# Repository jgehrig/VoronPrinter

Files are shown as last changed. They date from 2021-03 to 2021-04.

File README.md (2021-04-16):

# VoronPrinter
Build Logs, Notes, and Design Modifications for a Voron 3D Printer

## Cura Slicer Setup
[Cura Slicer Configuration](config/cura)

## Extended Feet
[Extended Printer Feet](mods/extended_feet)

## Power Entry Connector
[Power Entry Connector MountPCB](mods/power_entry)

## Wiring PCB
[Wiring Helper PCB](mods/wiring_pcb)

## X Gantry Endstop
[Adjustable X Gantry Endstop](mods/x_gantry_endstop)

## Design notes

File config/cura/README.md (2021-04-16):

# Voron V0 Cura Configuration
Setup instructions for Cura and the Voron V0.

Cura Screenshot with Voron Test Cube

These instructions were tested on Linux and Cura 4.8, they should also work on MacOS/Windows.

## Copy Configuration Folder
Find the Cura `Configuration Folder`:
 1. Open Cura.
 2. Using the file menu, `Help -> Configuration Folder`
 3. The `Configuration Folder` will open in your file manager

On Linux, the configuration folder is: `~/.config/cura/{cura_version}/`.

Simply copy the contents `cura-config-folder` from this repository into the path above.

## Adding Your Printer
Creates an instance of your printer in Cura.

Note, the Configuration Folder step above must be done before proceeding with the steps below.

Add your printer to Cura:
 1. In the file menu, `Settings -> Printer -> Add Printer...`.
 2. Select, `A non-networked printer -> VoronDesign -> VORON V0`.
 3. Type a unique `Printer name` in the text box on the right.
 4. Click the `Add` button.
 5. Set the `G-code flavor` dropdown to `Marlin`
 6. Paste your Start G-code, see [Startup GCode](#Startup-GCode).
 7. Modify any settings, the defaults should be fine.
 8. Click the `Next` button.
 9. You should see your pinter in the dropdown.

Screenshots:

Cura Add Printer Dialog <br />
Cura Machine Settings Dialog <br />
Cura Printer Dropdown <br />

## Printer Definition
Basic information about the printer is defined in:

`{cura_config_folder}/definitions/voron0_120.def.json`

```
{
    "name": "VORON V0",
    "version": 0,
    "inherits": "voron2_base",
    "metadata":
    {
        "visible": true,
        "platform": "V0_120mm_Bed.stl",
        "quality_definition": "voron2_base"
    },
    "overrides":
    {
        "machine_name":     { "default_value": "VORON V0" },
        "machine_width":    { "default_value": 120 },
        "machine_depth":    { "default_value": 120 },
        "machine_height":   { "default_value": 120 }
    }
}
```

## Print Platform 3D Model
The 3D model is definied in:

`{cura_config_folder}/meshes/V0_120mm_Bed.stl`

The STL model is courtesy of [hartk1213](https://github.com/VoronDesign/VoronUsers/blob/master/slicer_configurations/PrusaSlicer/hartk1213/V0/Bed_Shape/Model/V0_120mm_Bed.stl).

## Toolhead Definitions
A set toolheads with various nozzle sizes:
```
{cura_config_folder}/variants/voron0_120_v6_0.25.inst.cfg
{cura_config_folder}/variants/voron0_120_v6_0.30.inst.cfg
{cura_config_folder}/variants/voron0_120_v6_0.40.inst.cfg
{cura_config_folder}/variants/voron0_120_v6_0.50.inst.cfg
{cura_config_folder}/variants/voron0_120_v6_0.60.inst.cfg
{cura_config_folder}/variants/voron0_120_v6_0.80.inst.cfg
```

It is recommended to copy all toolheads, even if your printer only has one nozzle size available.

These files can be easily modified if your extruder has unique sizing/requirements.

Here is an example:
```
[general]
name = V6 0.40mm
version = 4
definition = voron0_120

[metadata]
setting_version = 16
type = variant
hardware_type = nozzle

[values]
machine_nozzle_size = 0.4
```

## Startup GCode
Start/End GCode runs before and after every printer, it is unique to your specific printer.

Here is an example for **Startup**:
```
G28                  ; home printer xyz
G0 Y0 X40            ; go to tongue of print bed
G1 Z0.2 F500.0       ; move bed to nozzle
G92 E0.0             ; reset extruder
G1 E4 F500.0         ; pre-purge prime LENGTH SHOULD MATCH YOUR PRINT_END RETRACT
G1 X80 E10.0 F500.0  ; intro line 1
G1 Y0.3              ; move in a little
G1 X40 E10.0 F500.0  ; second line
G92 E0.0             ; reset extruder
G1 Z2.0              ; move nozzle to prevent scratch
print_start
```
**NOTE:** The pre-purge prime (line 4) should match your printer's `~/printer.cfg`.

Usually the default `print_end` Stop GCode is enough.

These examples are courtesy of:

https://discord.com/channels/460117602945990667/696930677161197640/757703097949749399

## References
These setting are based on the following sources:
 - https://github.com/Ultimaker/Cura/blob/master/resources/definitions/voron2_base.def.json
 - https://github.com/Ultimaker/Cura/tree/master/resources/variants

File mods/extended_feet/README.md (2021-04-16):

# Voron V0 Extended Feet
Extended and improved feet for the Voron V0 Printer.

## Motivation
I needed more clearance underneath my printer for wiring. I was also frustrated by the stock feet
spinning out of alignment with the aluminum extrusions.

## Design
These parts were designed in Fusion360:
 - Rear Foot: https://a360.co/3dmuid4
 - Front Foot: https://a360.co/3tjqG18

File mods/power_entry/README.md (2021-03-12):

# Power Entry Connector Bracket
Yet another power entry connector bracket for the Voron V0.

## Motivation
This project was designed to work with connectors available in my parts bin. Yay MIT SwapFest!

## Design
This part was designed in Fusion 360:
https://a360.co/3bEmKl9

### BOM
A list of required parts for this build.

Required Parts:
 - 2 x M3 x 15mm BHCS
 - 2 x M3 T-Slot Nuts
 - TE/CORCOM 10CFS1 Power Entry Connector
 - (Printed) Mounting Bracket
 - (Printed) Face Plate

More details on the CORCOM Power Entry Connector:
 - [Digikey (Supplier)](https://www.digikey.com/en/products/detail/te-connectivity-corcom-filters/10CFS1/759031)
 - [TE Connectivity (Manufacturer)](https://www.te.com/usa-en/product-1-6609113-4.html)

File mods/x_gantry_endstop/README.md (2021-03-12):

# Voron V0 X Gantry Endstop
An adjustable X gantry endstop for the Voron V0.

## Motivation
The stock endstop did not reliably trigger on my printer. Occasionally, the toolhead would crash
before triggering the limit screw. The limit switch was also pressed very close to its fulcrum.

This custom endstop adds adjustment, and moves the contact point down the limit switch lever arm.

## Design
This part was designed in Fusion360:
https://a360.co/38s7iqe

The limit switch trigger position can be fine-tuned by rotating this part.

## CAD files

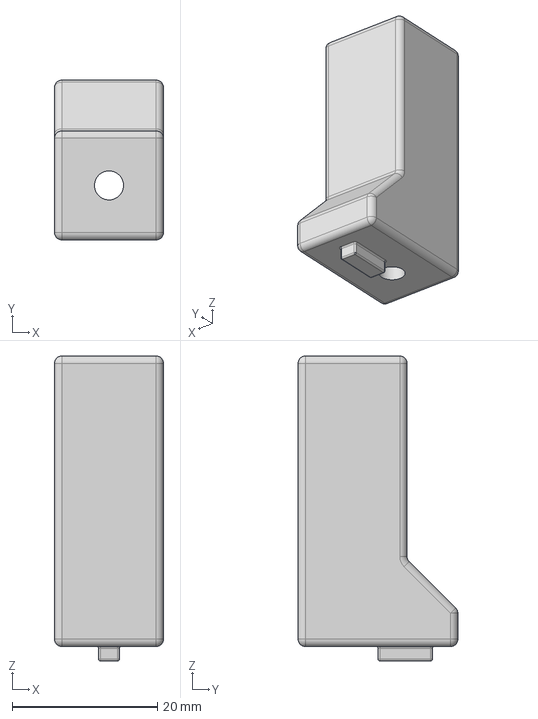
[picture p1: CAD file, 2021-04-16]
mods/extended_feet/CAD/Foot_Rear_Extended_Keyed.step
15.0 x 22.0 x 42.0 mm

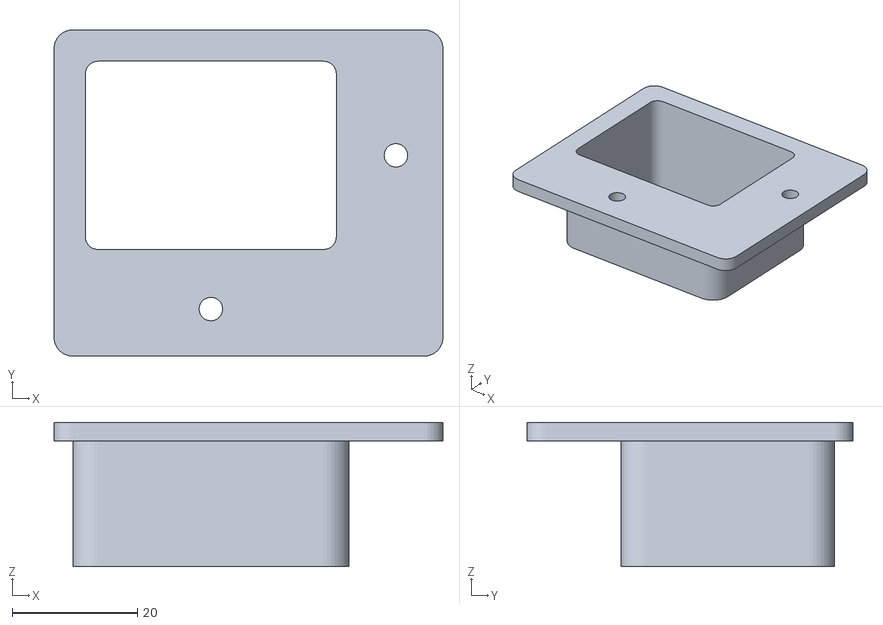
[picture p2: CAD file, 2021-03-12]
mods/power_entry/STL/PE_Bracket.stl
62.0 x 52.0 x 23.0

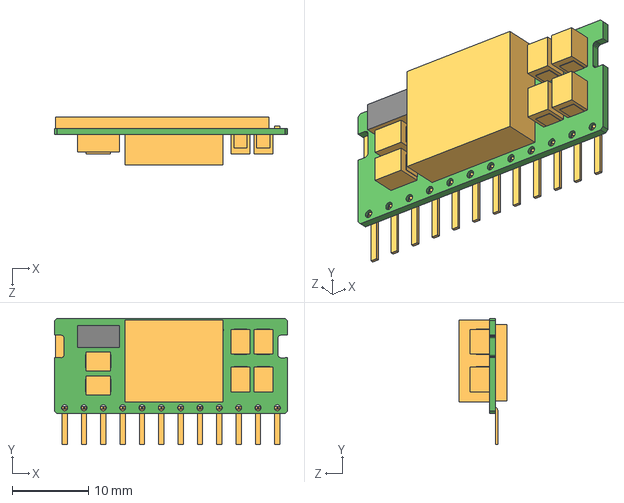
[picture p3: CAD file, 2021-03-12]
mods/wiring_pcb/CAD/3d_models/CUI_P783F-Q24-S5-S.step
30.6 x 16.6 x 6.30 mm

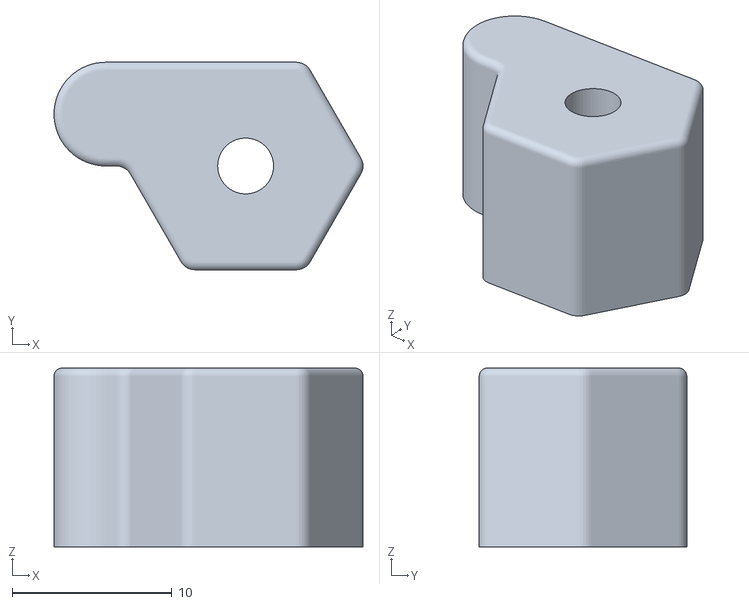
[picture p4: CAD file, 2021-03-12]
mods/x_gantry_endstop/STL/XGantryEndstop.stl
19.4 x 13.0 x 11.2

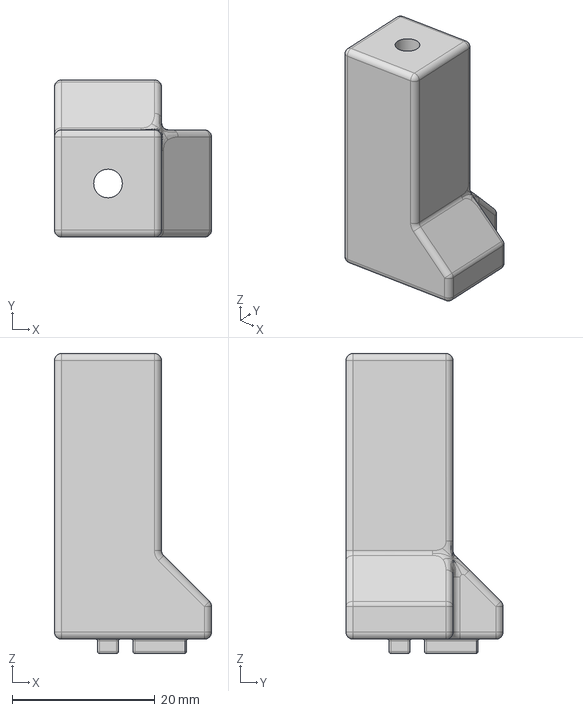
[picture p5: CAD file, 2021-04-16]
mods/extended_feet/CAD/Foot_Front_Extended_Keyed.step
22.0 x 22.0 x 42.0 mm

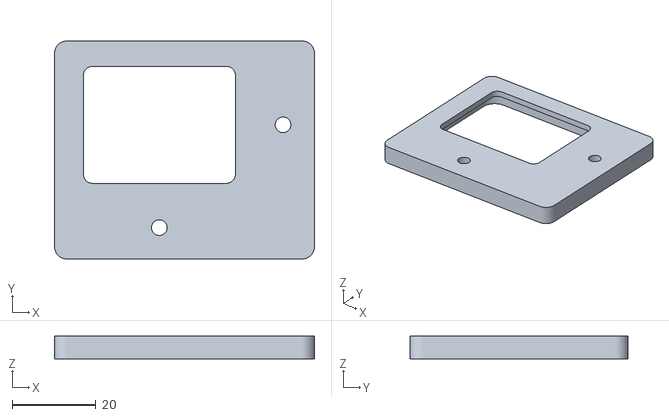
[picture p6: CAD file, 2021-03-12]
mods/power_entry/STL/PE_Faceplate.stl
62.0 x 52.0 x 5.47

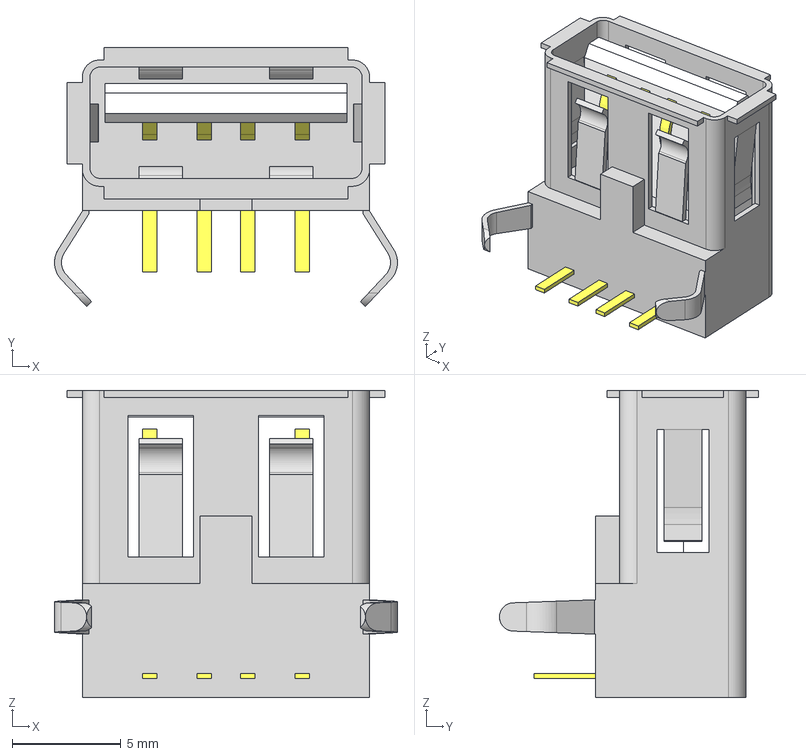
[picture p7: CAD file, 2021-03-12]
mods/wiring_pcb/CAD/3d_models/Connector_USB_A_Samtec.stp
15.7 x 11.9 x 14.1 mm
_USB-A-S-TH_S
_USB-A-S-W-TH_B
_USB-A-S-TH_P

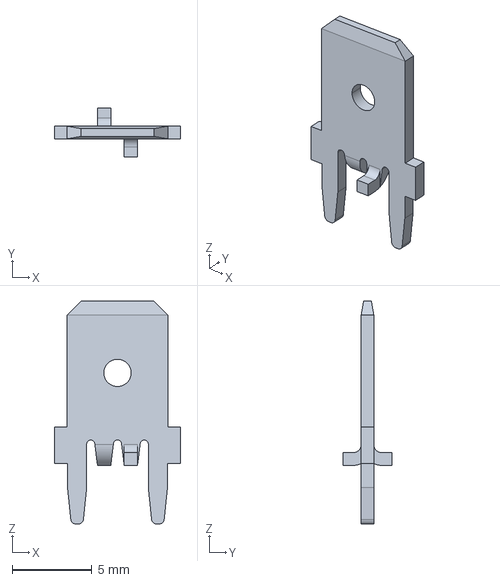
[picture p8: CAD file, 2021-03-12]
mods/wiring_pcb/CAD/3d_models/63824-1.step
7.92 x 3.09 x 14.0 mm

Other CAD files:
mods/extended_feet/CAD/Foot_Front_Extended_Keyed.f3d
mods/extended_feet/CAD/Foot_Rear_Extended_Keyed.f3d
mods/extended_feet/STL/Foot_Front_Extended_Keyed.stl
mods/extended_feet/STL/Foot_Rear_Extended_Keyed.stl
mods/x_gantry_endstop/CAD/XY_Gantry_Stop_Modified.f3d

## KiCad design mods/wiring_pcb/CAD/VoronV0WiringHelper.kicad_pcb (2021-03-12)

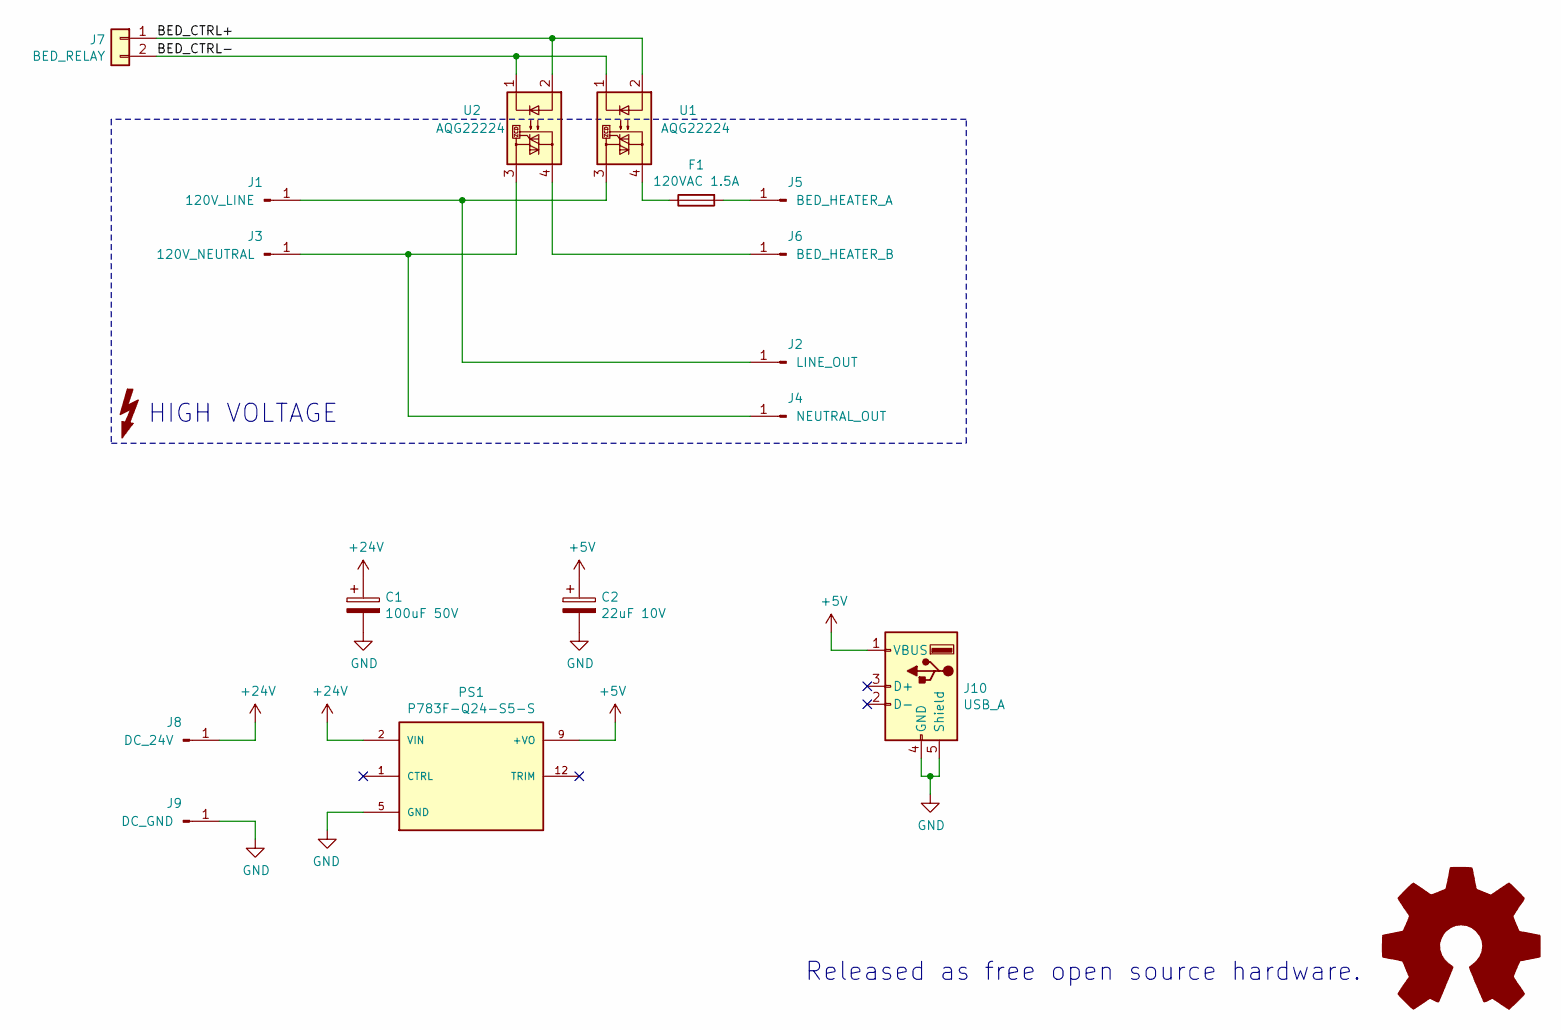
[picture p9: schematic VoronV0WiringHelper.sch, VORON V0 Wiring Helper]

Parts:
C1: 100uF 50V; CP_Radial_D8.0mm_P3.50mm
C2: 22uF 10V; CP_Radial_D5.0mm_P2.00mm
F1: 120VAC 1.5A; Fuseholder_Cylinder-5x20mm_Schurter_0031_8201_Horizontal_Op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
J1: 120V_LINE; CONN_63824-1
J2: LINE_OUT; CONN_63824-1
J3: 120V_NEUTRAL; CONN_63824-1
J4: NEUTRAL_OUT; CONN_63824-1
J5: BED_HEATER_A; CONN_63824-1
J6: BED_HEATER_B; CONN_63824-1
J7: BED_RELAY; JST_XH_B2B-XH-A_1x02_P2.50mm_Vertical
J8: DC_24V; CONN_63824-1
J9: DC_GND; CONN_63824-1
J10: USB_A; USB_A_CONNFLY_DS1095-WNR0
PS1: P783F-Q24-S5-S; CONV_P783F-Q24-S5-S; PARTREV 1.0
U1, U2: AQG22224

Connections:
+5V: C2.1, J10.1 (VBUS), PS1.9 (+VO), PS1.10 (+VO), PS1.11 (+VO)
+24V: C1.1, J8.1, PS1.2 (VIN), PS1.3 (VIN), PS1.4 (VIN)
/BED_CTRL+: J7.1, U1.2, U2.2
/BED_CTRL-: J7.2, U1.1, U2.1
GND: C1.2, C2.2, J9.1, J10.4 (GND), J10.5 (Shield), PS1.5 (GND), PS1.6 (GND), PS1.7 (GND), PS1.8 (GND)
unnamed: F1.1, U1.4
unnamed: F1.2, J5.1
unnamed: J1.1, J2.1, U1.3
unnamed: J3.1, J4.1, U2.3
unnamed: J6.1, U2.4

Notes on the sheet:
Released as free open source hardware.
HIGH VOLTAGE

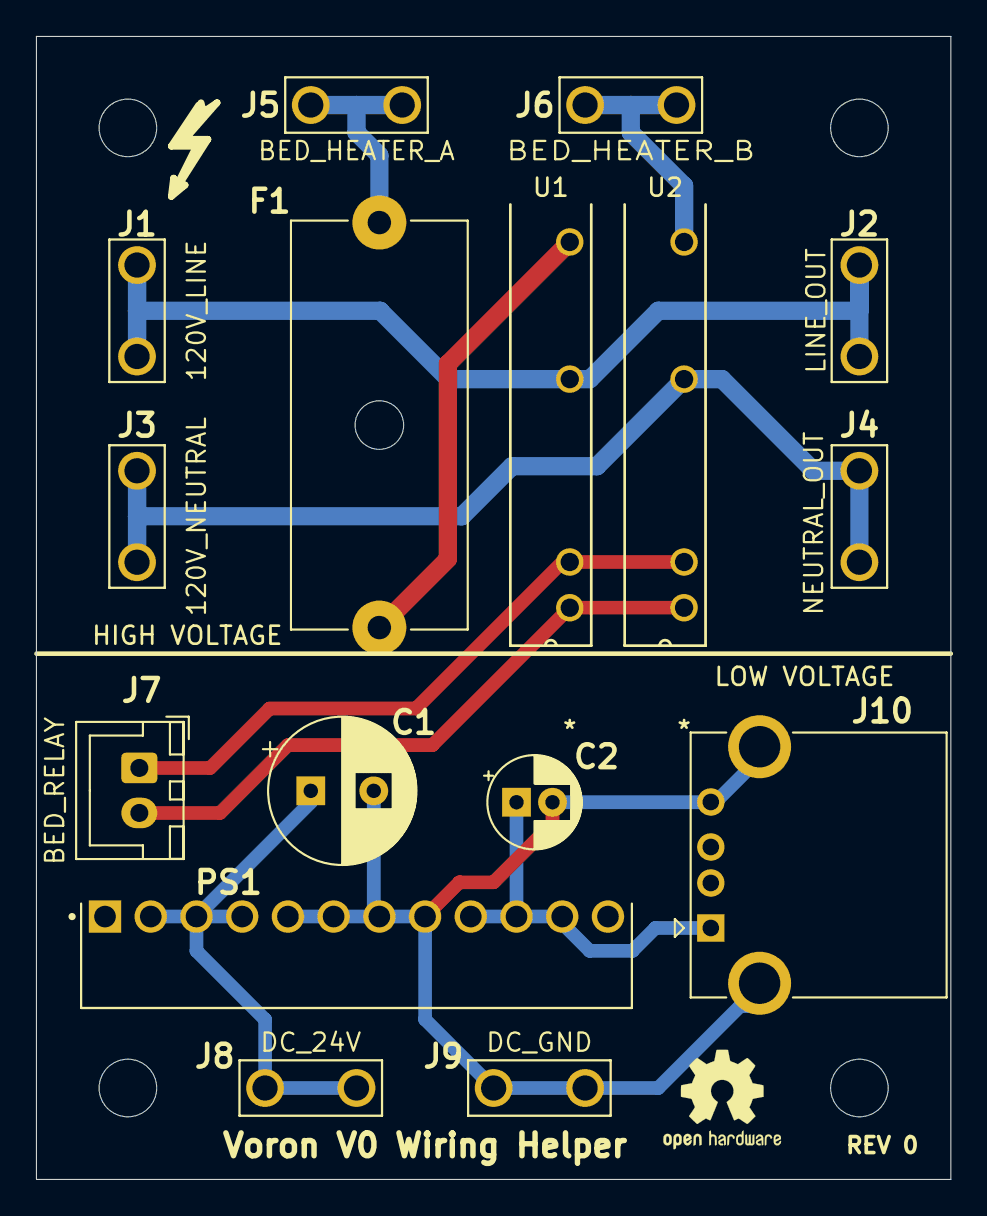
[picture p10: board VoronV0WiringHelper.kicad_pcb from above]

Board: 2 copper layers, 50.8 x 63.5 mm, 16 parts (0 on the bottom side), 10 nets.

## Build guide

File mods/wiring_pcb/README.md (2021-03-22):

# VORON V0 Wiring Helper PCB

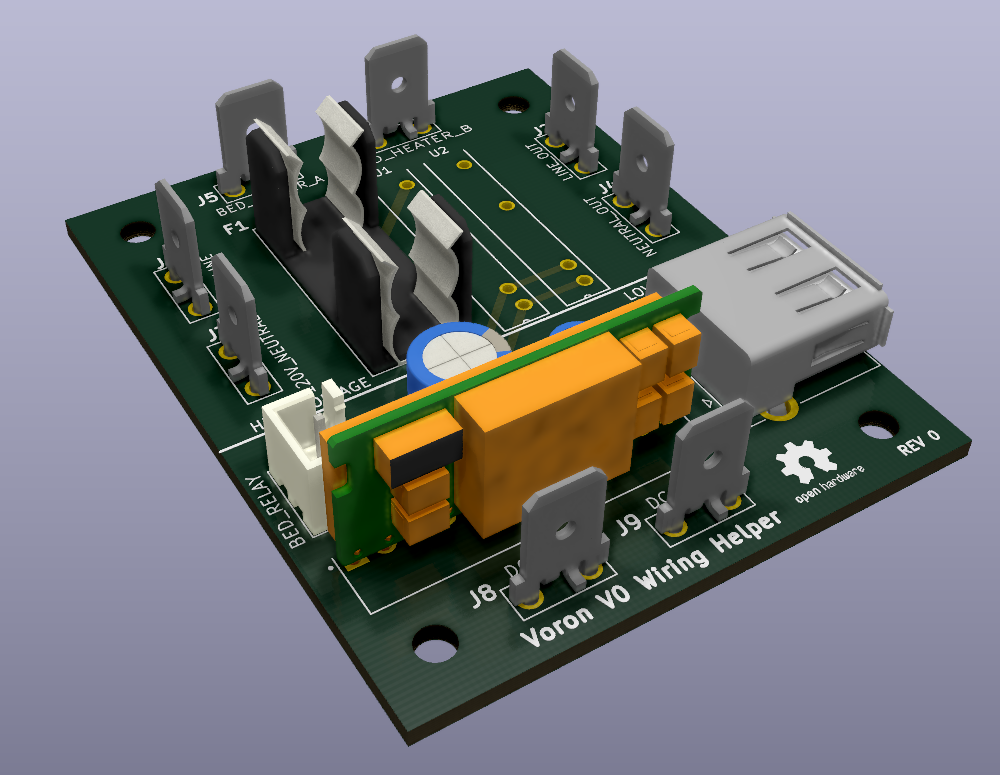
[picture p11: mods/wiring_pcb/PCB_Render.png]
PCB 3D Rendering


A PCB to simplify the mains wiring for a Voron V0.

**DISCLAIMER: Use at your own risk!**
This device is attached directly to 120V mains power. The electricity running through this device
can start fires, shock, injure, or even kill you. Please be careful!

I provide no warranty or guarantee as to the safety of this device. Use at your own risk.

## Motivation
The Voron V0 kit I purchased contained cheap electronics. The 120V mains relay for the heated bed
was unsafe. Instead of buying off-the-shelf electronics, I decided to build a PCB to simplify
the wiring. Cost is approximately the same as quality off-the-shelf components.

This device is responsible for:
 - Heated bed fusing.
 - 120VAC power split to the 24V PSU and heated bed.
 - Providing 5VDC USB power for the Raspberry Pi.

## Design
This PCB was designed in KiCad, free and open-source EDA software.

### PCB Fabrication
You should be able to order this board from any 2-layer PCB supplier.

Download the `GERBER` files, and upload them to you PCB supplier of choice.

Select the thickest copper plating available, the high-voltage traces carry ~1.25A @ 120VAC.

**Recommended PCB Fabricators:**
 - https://jlcpcb.com/ (Lowest Cost)
 - https://oshpark.com/ (Fast, Mid-Cost)
 - https://www.4pcb.com/ (Based in USA)

### BOM
Digikey part numbers are provided here, and in the schematic. All parts are commonly available,
and you should be able to order from any vendor (Mouser, Digikey, etc).

**Required electronic parts:**

| Ref | Qty | Description | Digikey P/N |
|---|-----|---|---|
| F1 |  1  | Fuse Holder | 732-11375-ND |
| F1 |  1  | 120VAC 1.5A Fuse | 507-1545-ND |
| J1-6  |  8  | PCB Spade Terminal | A29938CT-ND |
| J8 J9 | | | |
| J7 |  1  | JST 2-Pin Conn | 455-2273-ND |
| J10 |  1  | USB A Female Conn  | SAM10369-ND |
| U1,U2 |  2  | 24V SSR | PB1706-ND |
| PS1 |  1  | 24V to 5V DC/DC | 102-P783F-Q24-S5-S-ND |
| C1 |  1  | 50V 100uF | 1189-1860-ND |
| C2 |  1  | 25V 22uF | 1189-3984-ND |

[Order this BOM on Digikey](https://www.digikey.com/BOM/Create/CreateSharedBom?bomId=8479123)

The cost is ~$27 (USD) at the time of writing.

### Additional Notes
Recommended CUI PCB Footprint:
https://www.cui.com/product/resource/pcbfootprint/p783f-q24-s5-s

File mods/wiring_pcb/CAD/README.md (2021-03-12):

https://www.cui.com/product/resource/pcbfootprint/p783f-q24-s5-s

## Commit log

2021-03-12 Add X Gantry Endstop
    [XGantryEndstop.stl, XY_Gantry_Stop_Modified.f3d]
2021-03-12 Add Power Entry Bracket
    [PE_Bracket.stl, PE_Faceplate.stl]
2021-03-12 Add Voron Wiring Helper PCB
    [63824-1.step, CUI_P783F-Q24-S5-S.step, Connector_USB_A_Samtec.stp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]
2021-03-22 Add WiringHelper PCB image
    Update WiringHelper README, add image. Fixes table markdown.
2021-04-16 Add Extended Feet Mod
    This mod contains feet with additional space, and keying to the 1515
    extrusions. These feet were necessary to accommodate my wiring.
    [Foot_Front_Extended_Keyed.f3d, Foot_Front_Extended_Keyed.step, Foot_Front_Extended_Keyed.stl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]
2021-04-16 Add Cura Configuration Instruction
    Instructions for setting up Cura for use with a generic Voron V0
    Printer. Tested on Linux with Cura 4.8.

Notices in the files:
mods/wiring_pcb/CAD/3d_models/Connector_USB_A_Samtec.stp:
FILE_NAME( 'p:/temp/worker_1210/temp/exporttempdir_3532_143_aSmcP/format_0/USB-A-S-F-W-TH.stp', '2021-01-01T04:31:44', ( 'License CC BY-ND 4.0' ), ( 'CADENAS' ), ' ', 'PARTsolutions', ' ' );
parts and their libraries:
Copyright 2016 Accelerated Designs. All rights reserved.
